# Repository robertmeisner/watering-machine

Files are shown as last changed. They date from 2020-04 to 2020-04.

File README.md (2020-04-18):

# Watering Machine

Modular Watering Machine (Arduino compatible) which allows you to water your crops/plants when needed and provide grow lights on specified interval.

## Introduction

It's an automatic plant watering system or smart irrigation system.

Main functionalities:

- monitors soil moisture with multiple moisture sensors
- waters the plants on specified intervals
- waters plants when soil moisture gets below certain treshold
- turns on grow lights on specified intervals and with specified duration
- allows you to configure and adjust moisture/watering/lighting duration/tresholds

Library aims to be platform agnostic (can be run on Arduino compatible devices: Arduino, ESP32, ESP8266, etc)

Interface with physical layer is separated from Watering Machine "business" logic.
Functions responsible for interfacing with physical infrastructure are injected into components upon their creation.

### States

Watering Machine
Change of states can be triggered with WateringMachine's commands:
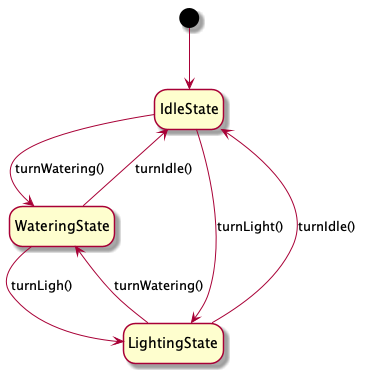
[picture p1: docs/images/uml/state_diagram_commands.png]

or when certain conditions are met:
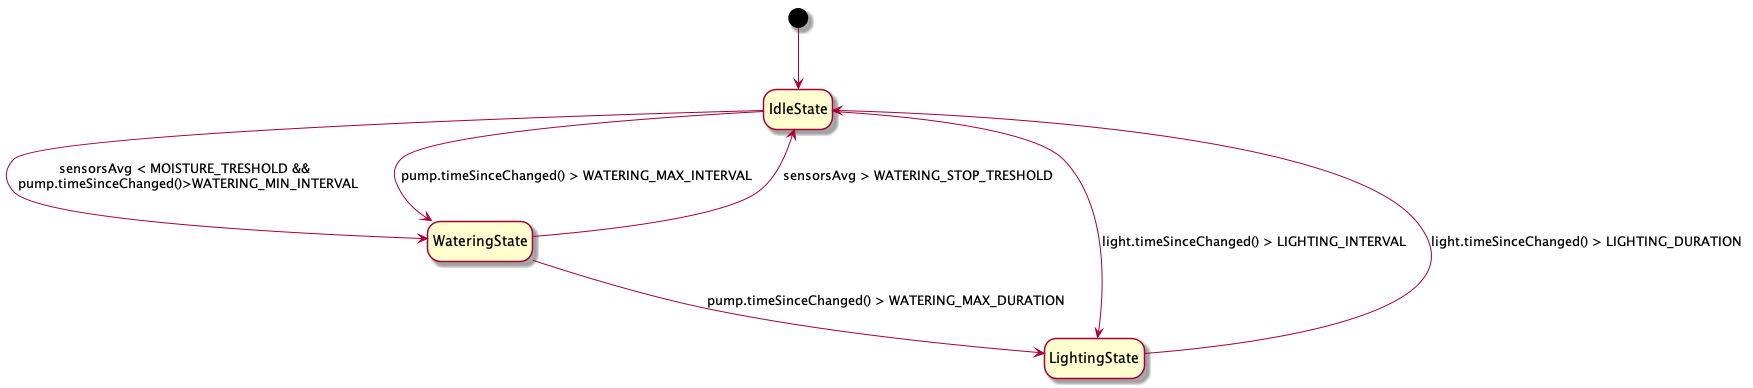
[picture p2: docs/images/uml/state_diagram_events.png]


Note: Lighting and Watering states are separate and cannot occur in parallel.

## Usage guide

### Configuration

Watering Machine behaviour can be cotnroller with the WateringMachineConfig object.
All times are in milliseconds.

Example Arduino code:

```cpp
WateringMachineConfig config;
setup(){
    const unsigned long ONE_HOUR = 1000 * 60 * 60; // hour constant

    config.LIGHTING_DURATION = ONE_HOUR * 8; // How long lighting session should last
    config.LIGHTING_INTERVAL = ONE_HOUR * 16; // Interval between lighting sessions
    config.WATERING_MAX_DURATION = ONE_HOUR /2; // How long watering should last
    config.WATERING_MAX_INTERVAL = ONE_HOUR * 24 * 7; // Maximal interval between waterings. After that time, watering will start even if avarage moisture level from sensors is over the MOISTURE_TRESHOLD
    config.WATERING_MIN_INTERVAL = ONE_HOUR; // Minimal interval between waterings. After watering is done it won't start again, before WATERING_MIN_INTERVAL has passed,even if avarage moisture level from sensors is below the MOISTURE_TRESHOLD
    config.MOISTURE_TRESHOLD = 52; //if avarage moisture level from sensors is below the MOISTURE_TRESHOLD watering starts
    config.WATERING_STOP_TRESHOLD = 80; //watering will stop if avarage moisture level from sensors reaches that value
}
```

### Sensors adjustment

1. Set DebugLevel to Debug: cLogSetDebugLevel(DebugLevel::DEBUG)
2. Run your Watering Machine
3. Check raw value for sensors when put into Water or wet ground, adjust sensorWetRawValue for sensor in ControlFunctions file
4. Check raw value for sensors when hold in Air or put into dry ground, adjust sensorDryRawValue for sensor in ControlFunctions file

### Arduino

### Example code

```cpp

// include components
#include "src/WateringMachine/Components/PulsePump.h"
#include "src/WateringMachine/Components/Light.h"
#include "src/WateringMachine/Components/MoistureSensor.h"
// include State factory (class geenrating states of Watering Machine)
#include "src/WateringMachine/States/StateFactory.h"
// include config class
#include "src/WateringMachine/WateringMachineConfig.h"
// include Watering Machine
#include "src/WateringMachine/WateringMachine.h"
// include Control Functions used to interface with hardware. Those are injected into Components' constructors.
#include "src/Firmware/Arduino/ControlFunctions.v1.h"

// config object instantiated
WateringMachineConfig config;
// pointer to WateringMachine
WateringMachine *wateringMachine;
// create pump object
static PulsePump pump(startPumpFunc, stopPumpFunc, initPumpFunc); //static so they wont be deleted after setup is detroyed
// create light object
static Light light(lightOnFunc, lightOffFunc, lightInitFunc);
/**
 * Arduno setup function
 */
void setup()
{
    // initialize the serial communication:
    Serial.begin(115200);
    const unsigned long ONE_HOUR = 1000 * 60 * 60; // hour constant

    config.LIGHTING_DURATION = ONE_HOUR * 8;          // How long lighting session should last
    config.LIGHTING_INTERVAL = ONE_HOUR * 16;         // Interval between lighting sessions
    config.WATERING_MAX_DURATION = ONE_HOUR / 2;      // How long watering should last
    config.WATERING_MAX_INTERVAL = ONE_HOUR * 24 * 7; // Maximal interval between waterings. After that time, watering will start even if avarage moisture level from sensors is over the MOISTURE_TRESHOLD
    config.WATERING_MIN_INTERVAL = ONE_HOUR;          // Minimal interval between waterings. After watering is done it won't start again, before WATERING_MIN_INTERVAL has passed,even if avarage moisture level from sensors is below the MOISTURE_TRESHOLD
    config.MOISTURE_TRESHOLD = 52;                    //if avarage moisture level from sensors is below the MOISTURE_TRESHOLD watering starts
    config.WATERING_STOP_TRESHOLD = 80;               //watering will stop if avarage moisture level from sensors reaches that value
    // Create sensor objects and add them to a vector
    static std::vector<MoistureSensor> sensors;
    sensors.push_back(MoistureSensor(Sensor1ReadFunc, sensorInitFunc));
    sensors.push_back(MoistureSensor(Sensor2ReadFunc, sensorInitFunc));
    // initialize StafeFactory object
    static StateFactory sf;
    //create a WateringMachine object
    wateringMachine = new WateringMachine(config, sf, light, pump, sensors);
    //init the WateringMachine
    wateringMachine->init();
};
/**
 * Arduino loop function
 */
void loop()
{
    // call tick function every time to handle WateringMachine logic
    wateringMachine->tick();
    // delay 5s
    delay(5000);
};

```

#### Example Schematic and Bill of Material

##### ESP8266

- [ESP8266 Bill of Material with links](./docs/bom/ESP82666_bom.md)

**Schematic:**
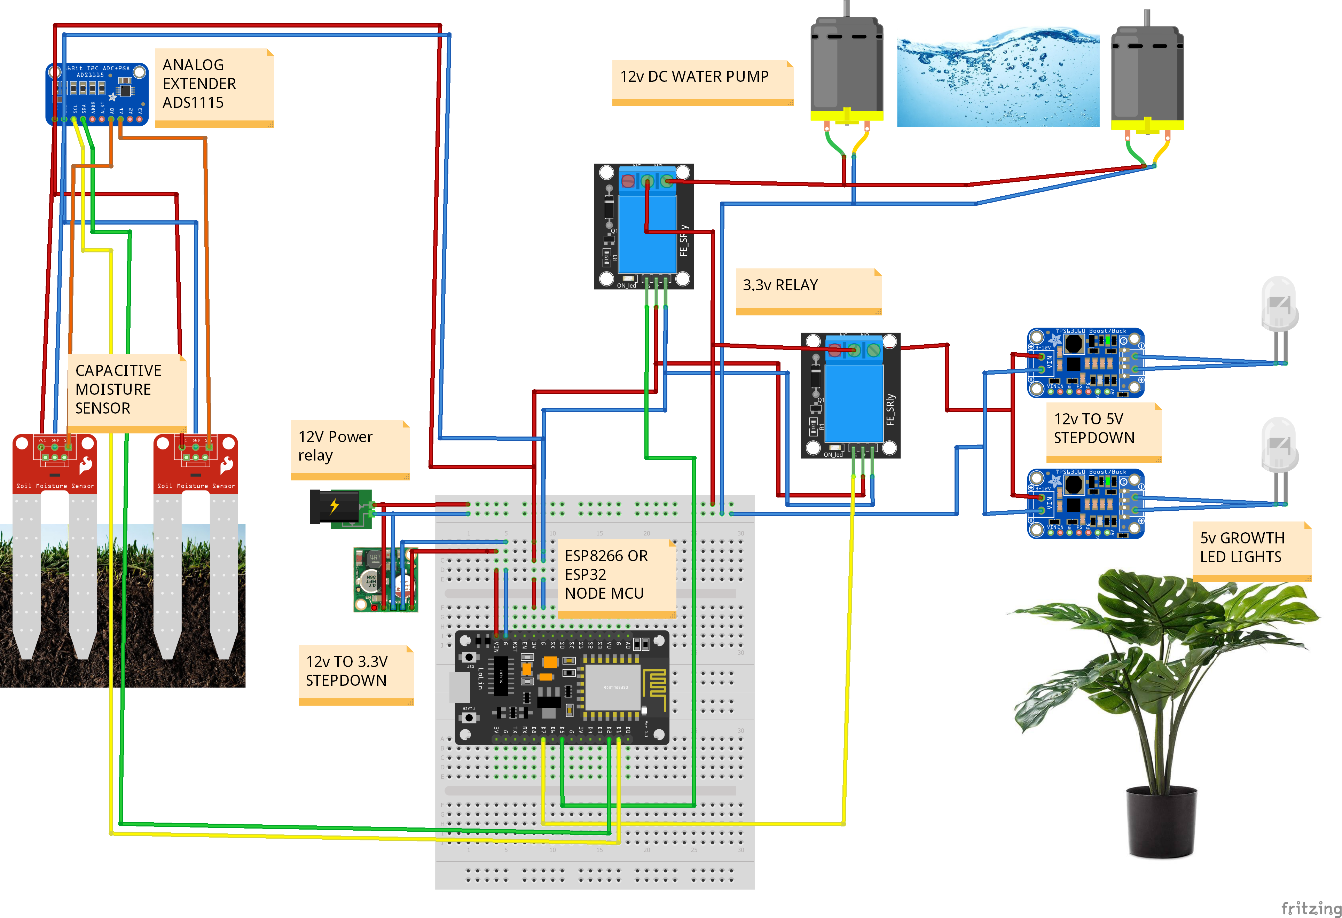
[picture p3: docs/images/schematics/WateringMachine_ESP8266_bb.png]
ESP8266


#### Test/Evaluate/Understand the code

1. Clone or download this repository
2. Uncomment the line // #define WATERING_TEST 1 in watering-machine.ino
3. Open watering-machine.ino inArduino IDE
4. Connect Arduino compatible device to USB port
5. Set port to correct value
6. Click Upload
7. After upload has finished open Serial Terminal and set baud rate to 115200
8. You can see now logs printed by Watering Machine
9. You can experiment with different values returned by Control function, reupload the code and see how this influences the behaviour

#### Run on your own device and setup

1. Build/prototype your Watering Machine (see example Schematic and Bill of Materials)
2. Clone or download this repository
3. Rename root folder e.g. my_watering_machine
4. Duplicate /watering-machine.ino and rename it to mywaterin_machine.ino
5. Copy /src/Firmware/Arduino/ControlFunctions.v[x].h to /libraries/Arduino/ControlFunctions.v[x].h folder
6. change include path of ControlFunctions.v[x].h to the new one
7. Adjust pin numbers in ControlFunctions file to match your build

## Use Cases

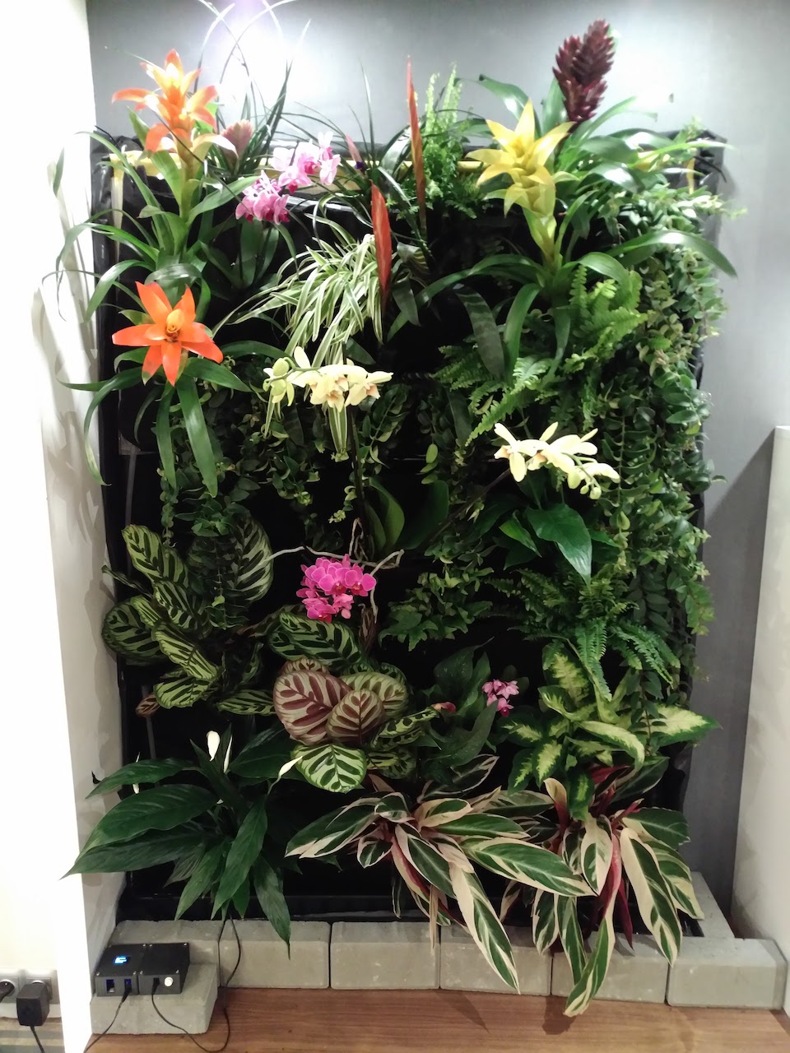
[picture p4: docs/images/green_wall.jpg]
Green Wall in your appartment


## Project structure

``` folder
.
├── docs - documentation and other file assets (images, uml etc)
├── libraries - Here you can place some aditional libraries if needed
├── src - Waterng Machine code
│   ├── Firmware - Control Functions which allow to communicate with a hardware/physical components. Those are injected to component objects upon their creation.
│   │   ├── Arduino - Arduino compatible examples of Control functions
│   │   └── ControlFunctions.Test.h - Test Control Functions to experiment with
│   └── WateringMachine/
│       ├── Components/ - concerte classes of the components (sensors, pump, lights etc.)
│       │   └── StateMachineInterfaces/ - Abstract Component state MAchine classes to be derived by concerte component classes.
│       ├── States/ - Watering MAchine State classes (Watering, Idle, Lighting)
│       ├── Utils/ - Utility classes (logs, formatting, etc. )
│       ├── WateringMachine.cpp
│       ├── WateringMachine.h - main control class of the Watering Machine
│       └── WateringMachineConfig.h 
└── watering-machine.ino - example Arduino sketch with fulll configuration
```

## Improvements and changes

## Questions

For questions about the usage of the libraries, please fill in an issue labeled "question" in Github as that makes it far easier to track them.

## Bugs and issues

For bugs in the libraries, please fill in an issue in Github as that makes it far easier to track them. If possible provide a minimal code snippet that exposes the bug. Also proposals for solutions are welcome.
Issues are not bugs but still possible problematic. E.g. if a library is too slow for your application that is an issue, not a bug. Please fill in an issue and provide as much details about your requirements.

## License and Warranty

Apache License
Version 2.0, January 2004
[http://www.apache.org/licenses/](http://www.apache.org/licenses/)

Please check the file LICENSE and NOTICE for the details.
Give credits a it's requried by the license and if you want to donate, please donate to charity like "doctors without borders".

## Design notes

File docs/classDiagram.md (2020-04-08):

# Class diagrams

## States

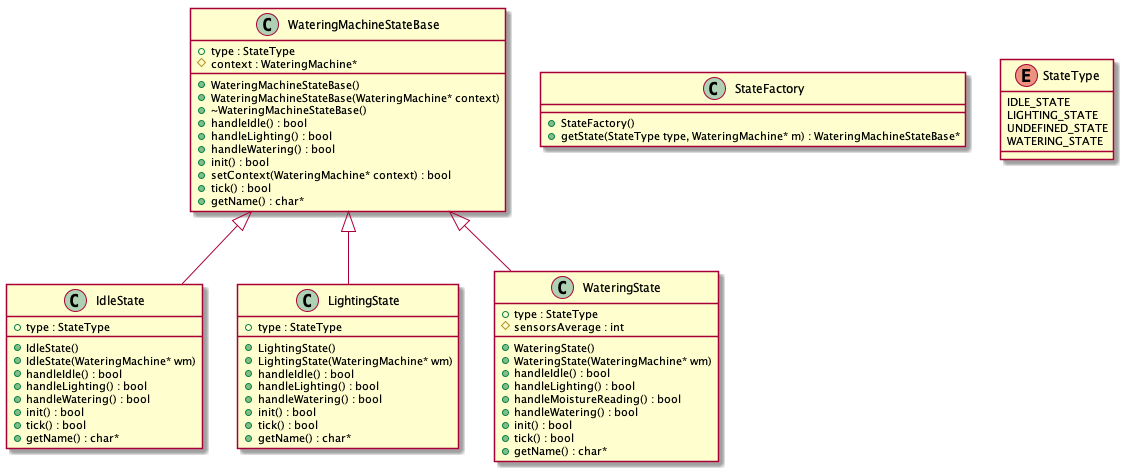
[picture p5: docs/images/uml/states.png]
Watering Machine States Class Diagram

## Components

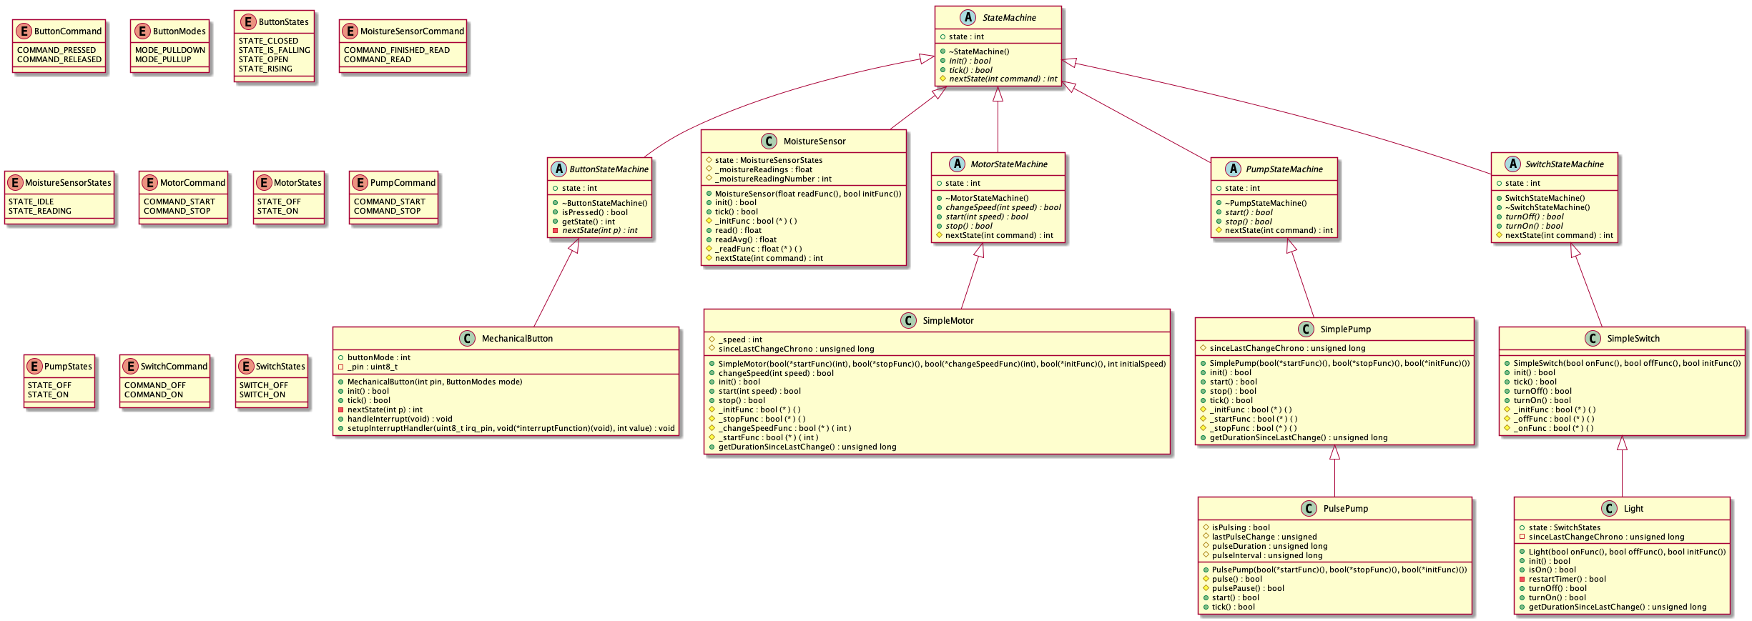
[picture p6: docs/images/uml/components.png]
Watering Machine Components Class Diagram

## Everything

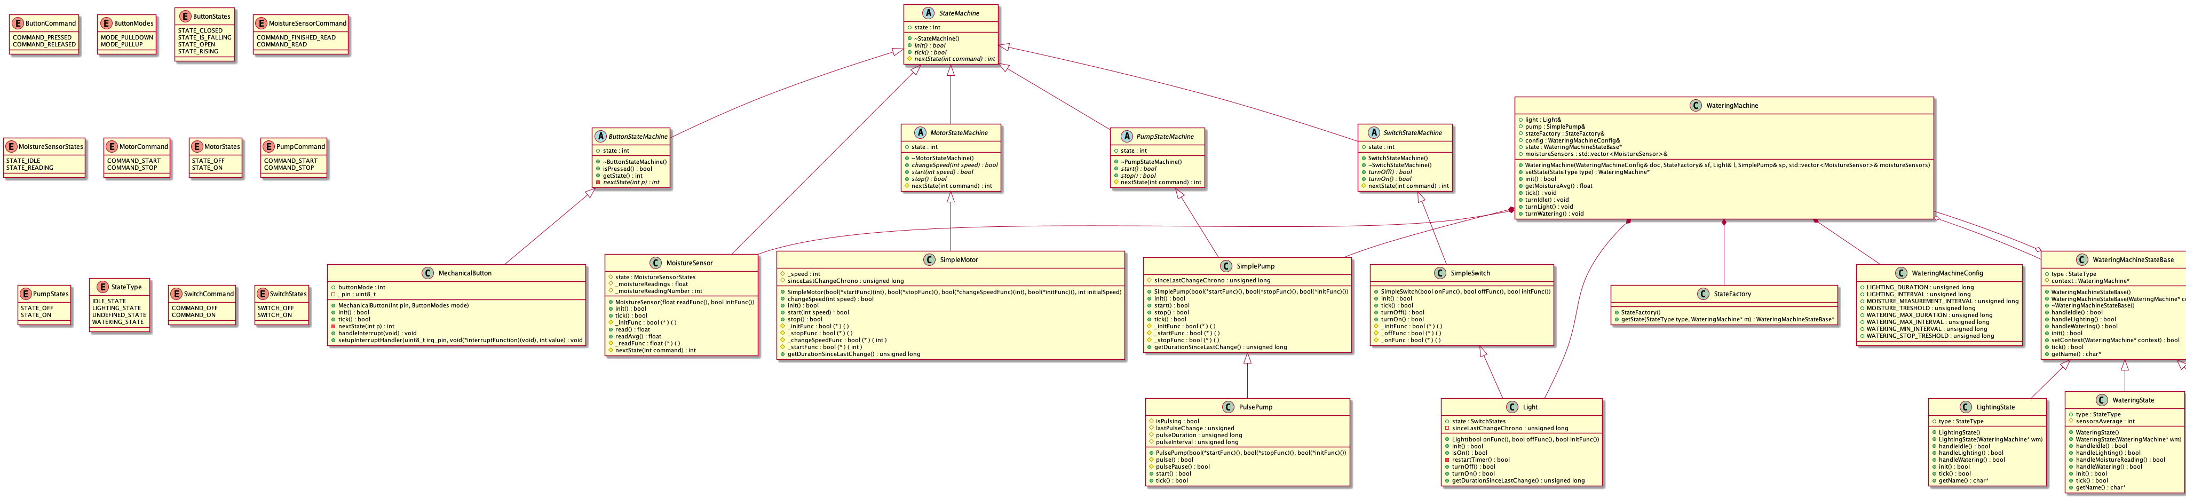
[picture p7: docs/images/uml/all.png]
Watering Machine Class Diagram


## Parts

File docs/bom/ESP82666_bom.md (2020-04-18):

# Greaan Wall + Watering Machine + ESP8266 Node Mcu Bill of Material

*Note:* Below you can find affiliate links, buying from those you support development of this library.

## Water Pump

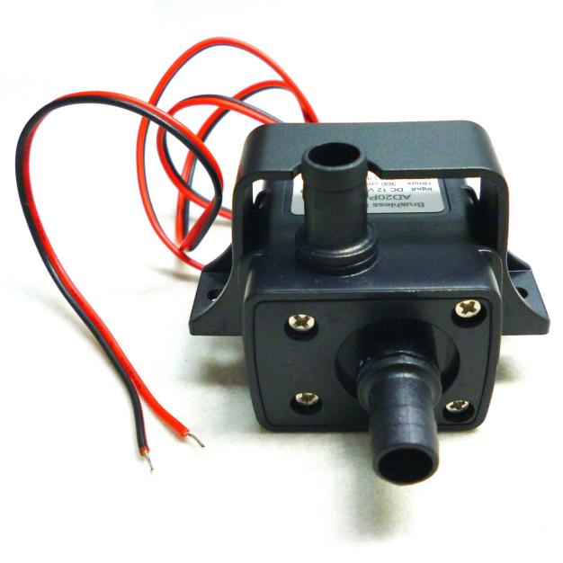
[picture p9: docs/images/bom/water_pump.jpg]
Water Pump 12V


- DC12V pump mini brushless dc submersible pump water cycle cooling [AliExpress.com Product](https://s.click.aliexpress.com/e/_Bf9Lvmsu) </a>

## Moisture sensors

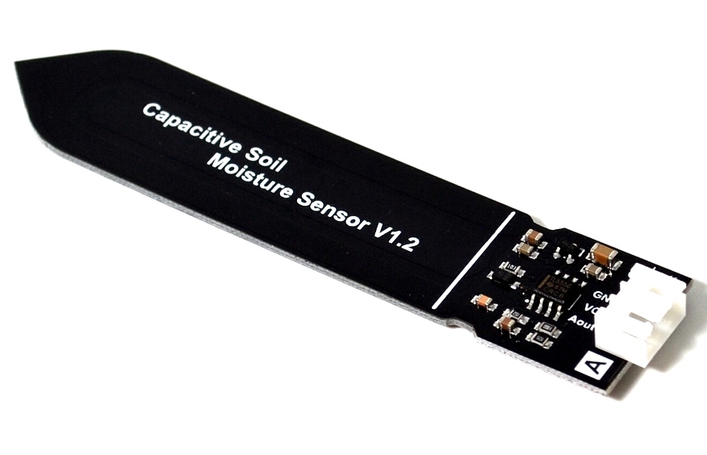
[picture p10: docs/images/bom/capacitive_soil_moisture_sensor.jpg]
Moisture sensors


- Capacitive soil moisture sensor not easy to corrode wide voltage wire for arduino [AliExpress.com Product](https://s.click.aliexpress.com/e/_d76ytBS" target="_parent">AliExpress.com Product - 10pcs</a>

## Analog extender ADS1115

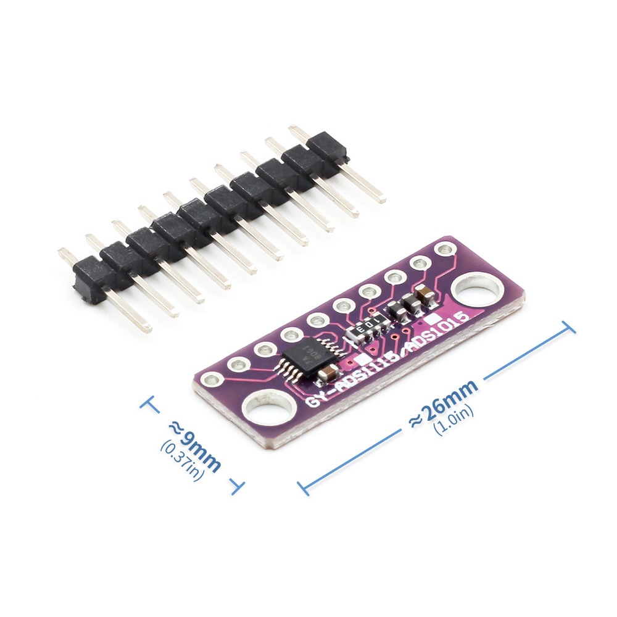
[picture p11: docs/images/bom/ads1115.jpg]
ADS1115


- I2C ADS1115 16 Bit ADC 4 channel Module with Programmable Gain Amplifier 2.0V to 5.5V [AliExpress.com Product](https://s.click.aliexpress.com/e/_dXel4C0)

## 3.3V Relays

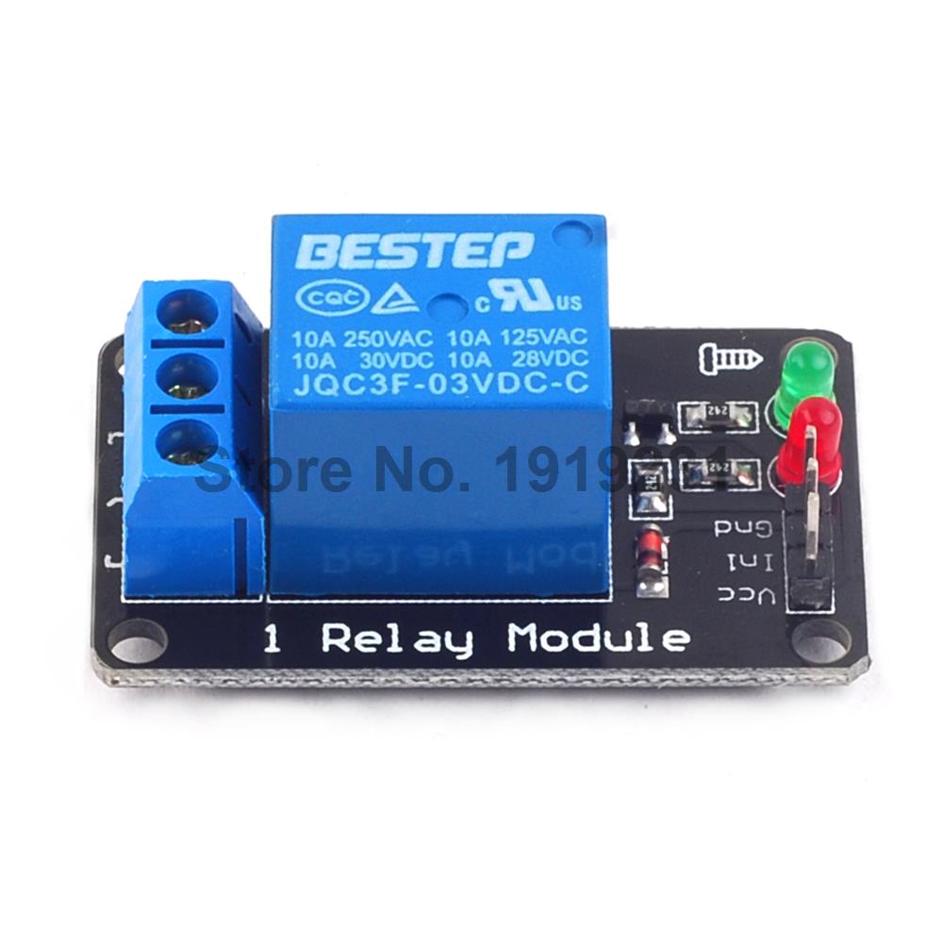
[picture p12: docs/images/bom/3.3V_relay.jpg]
3.3V Relays


- Thyristor AC Switch (relay), 3.3V/5V logic, AC 220V/5A (peak 10A) [AliExpress.com Product](https://s.click.aliexpress.com/e/_d8EjZzI)
- 3.3V 5V 12V 24V Low Level Trigger 1 Channel Relay Module Interface Board Shield for PIC AVR DSP ARM MCU Arduino [AliExpress.com Product](https://s.click.aliexpress.com/e/_dZJLRYU)

## ESP8266 module

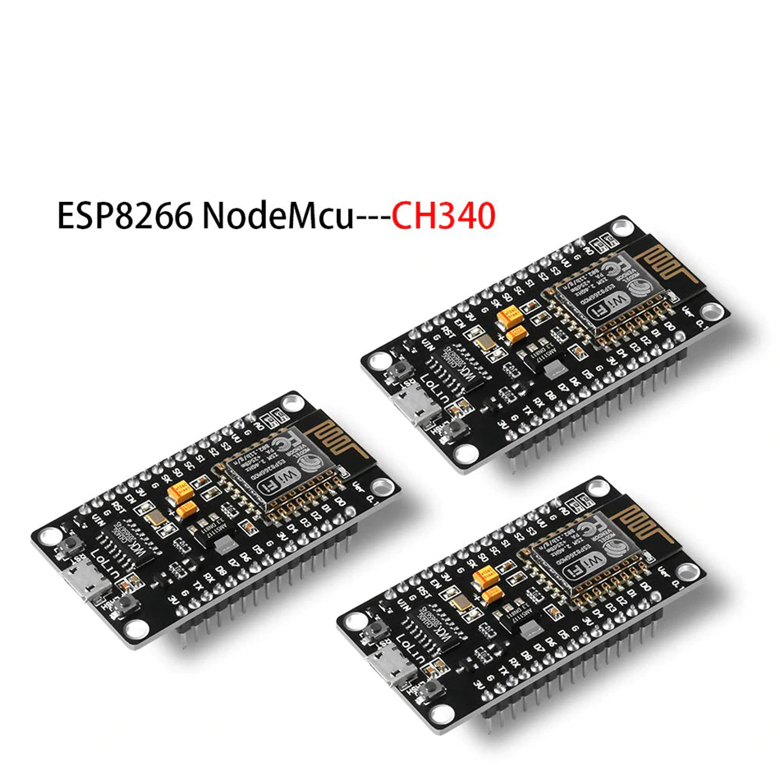
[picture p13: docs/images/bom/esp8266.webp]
ESP8266 module


- L293D Motor Shield Board Wireless Wifi Esp8266 Esp-12E Node MCU Development Kit NodeMCU Rc Toy Remote Control IoT Smart Car [AliExpress.com Product](https://s.click.aliexpress.com/e/_dXiRNkc)
- ESP32 Development Board ESP-32 ESP-32S ESP 32S Lua WiFi Bluetooth Node MCU Board IOT For LuaNode NodeMcu NodeMCU-32S ESP32 S [AliExpress.com Product](https://s.click.aliexpress.com/e/_BfZLenyU)

## ESP8266 development board

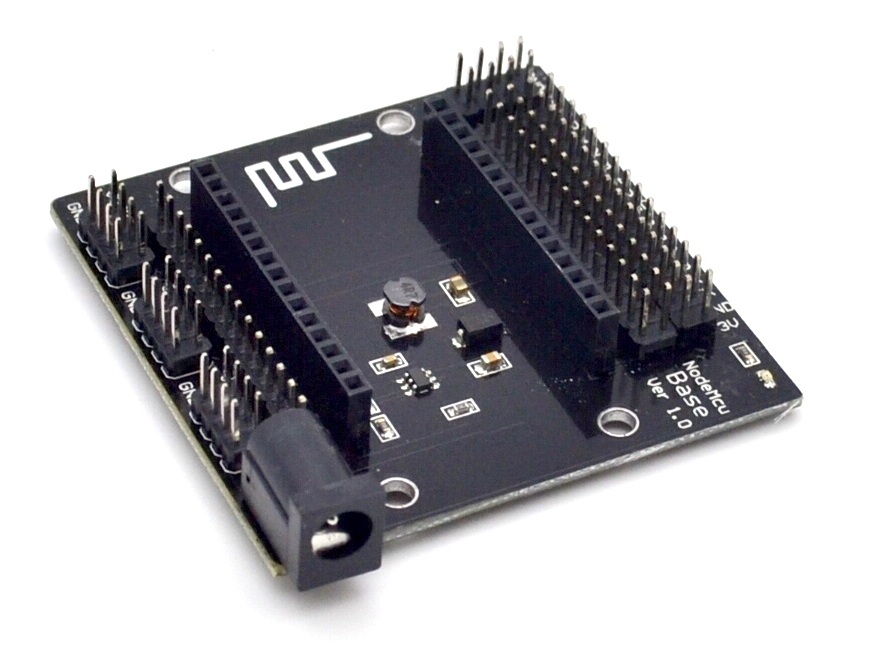
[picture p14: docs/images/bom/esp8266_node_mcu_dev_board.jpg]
ESP8266 development board


- NodeMcu Node MCU Base ESP8266 Testing DIY Breadboard Basics Tester suitable for NodeMcu V3 [AliExpress.com Product](https://s.click.aliexpress.com/e/_d89DjJa)

## 12V power source

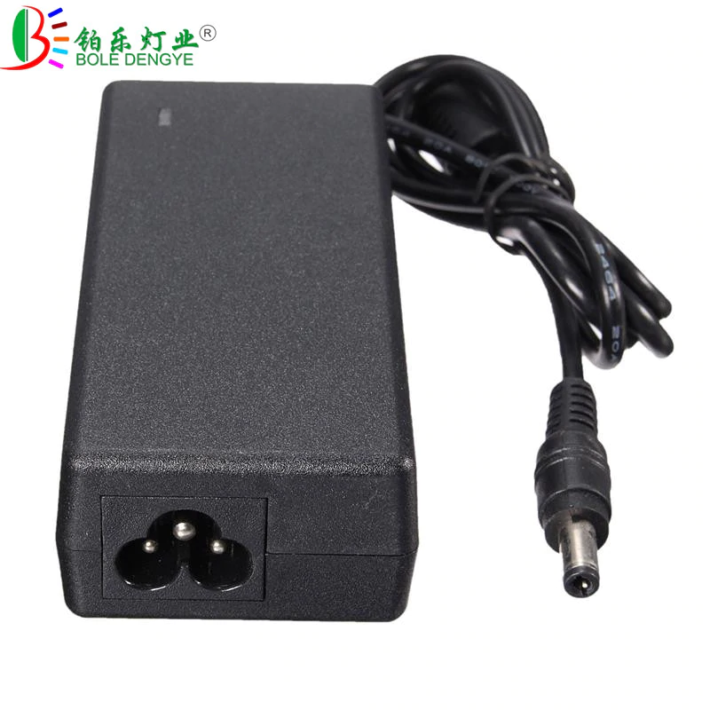
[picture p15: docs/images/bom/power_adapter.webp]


- Power Adapter Supply AC 110V/220V To 12V  Transformer 3A 5A 6A 8A 10A [AliExpress.com Product](https://s.click.aliexpress.com/e/_dWtz1GU)

## 8mm hose, filter and connectors

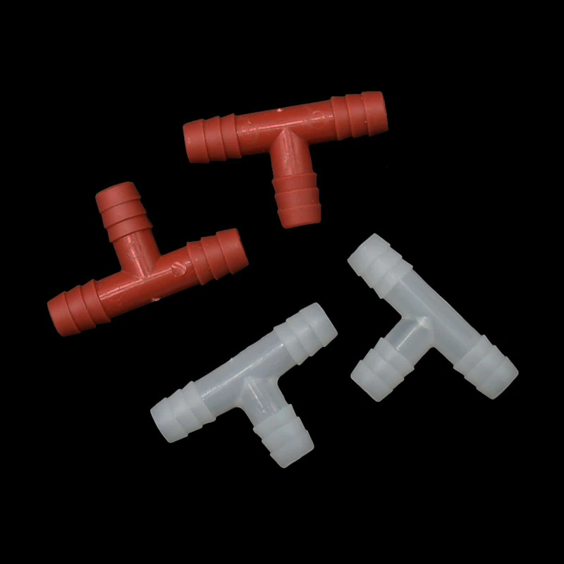
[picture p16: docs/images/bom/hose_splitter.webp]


- T way T-Shape Brass Barb Pipe Hose Fitting 3 way connector For 4mm 5mm 6mm 8mm 10mm 19mm hose copper Pagoda Water Tube Fittings [AliExpress.com Product](https://s.click.aliexpress.com/e/_dV8zvJ6)
- 2pcs Venturi Hose Filter Agricultural Water Purifier Industrial Filter 3 / 8mm Hose Accessory Garden Tools Fountain Accessory [AliExpress.com Product](https://s.click.aliexpress.com/e/_d8sxiRe)
- 3/5mm 4/7mm 8/11mm New PVC Garden Water Hose Irrigation Watering Tubing 1/8'' 1/4'' 3/8'' Black White Blue Transparent Hose [AliExpress.com Product](https://s.click.aliexpress.com/e/_dS1djpq)

## Growth light and stepdown module

ESP8266 development board

- Phytolamps for Plants 5V LED Grow Light Strip 2835 Chip 0.5m 1m 2m LED Phyto Tape for Hydroponic Greenhouse Seedlings Growth [AliExpress.com Product](https://s.click.aliexpress.com/e/_dYde1VQ)
- USB Phytolamps for Plants 5V LED Grow Light Strip 2835 Chip 0.5m 1m 2m LED Phyto Tape for Hydroponic Greenhouse Seedlings Growth [AliExpress.com Product](https://s.click.aliexpress.com/e/_d7z4tj6)
- Plant Grow Light Full Spectrum LED Strip Flower Phyto Lamp Red Blue 10:4 Cultivation Indoor Lamp For Desktop Plant Flower USB UV [AliExpress.com Product](https://s.click.aliexpress.com/e/_d8Ijb2C)
- LM2596s DC-DC step-down power supply module 3A adjustable step-down module LM2596 voltage regulator 24V 12V 5V 3V [AliExpress.com Product](https://s.click.aliexpress.com/e/_dSJVG56)

## Plastic/nylon zip ties

- Self-locking plastic nylon tie 100 PCS black 5X300cable tie fastening ring3X200 cable tie zip wraps strap nylon cable tie [AliExpress.com Product](https://s.click.aliexpress.com/e/_dVu9dCy)

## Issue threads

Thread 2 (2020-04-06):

Improve README.md

robertmeisner, 2020-04-06:
Documentation should include:

- Introduction
- Installation guide
- Improvements and changes
- Questions
For questions about the usage of the libraries, please post a question on???
- Bugs and issues
For bugs in the libraries, please fill in an issue in Github as that makes it far easier to track them. If possible provide a minimal code snippet that exposes the bug. Also proposals for solutions are welcome.
Issues are not bugs but still possible problematic. E.g. if a library is too slow for your application that is an issue, not a bug. Please fill in an issue and provide as much details about your requirements.
- License and Warranty
I appreciate if you give credits when appropriate, and if you want to donate, please donate to charity like "doctors without borders".
Please check the file LICENSE and NOTICE for the details.

robertmeisner, 2020-04-18:
Should add example BoM for esp8266

Closed 2020-04-18.

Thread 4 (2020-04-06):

Fix log message in Watering state

robertmeisner, 2020-04-06:
When moisture sensor average is below MOISTURE_TRESHOLD  the message looks stange:
`Moisture sensor is between MOISTURE_TRESHOLD and WATERING_STOP_TRESHOLD: 80>20<40`
should be
`Moisture sensor is between below: WATERING_STOP_TRESHOLD: 20<80. Watering duration is below WATERING_MAX_DURATION: 120000<33223232`

Closed 2020-04-07.

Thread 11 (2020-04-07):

WiFi interface

robertmeisner, 2020-04-07:
**Is your feature request related to a problem? Please describe.**
I'm always frustrated when i have to connect , WIFI functionality would be nice

**Describe the solution you'd like**

- It should be possible to expose control panel through WIFI with user interface (local http server) or MQTT server (subscribe and publish).
- WIFI should be optional.
- User should be able to:
  - update configuration
  - turn Watering on/off
  - turn Light on/off
  - read sensor values

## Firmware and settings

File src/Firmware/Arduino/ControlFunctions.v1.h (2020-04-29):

#include <Arduino.h>
#include <Wire.h>
#include <Adafruit_ADS1015.h>
// Include custom log library
#include "../../WateringMachine/Utils/CustomLog.h"

#ifndef ArduinoFunctions_h
#define ArduinoFunctions_h
// The ADC input range (or gain) can be changed via the following
// functions, but be careful never to exceed VDD +0.3V max, or to
// exceed the upper and lower limits if you adjust the input range!
// Setting these values incorrectly may destroy your ADC!
//                                                                ADS1015  ADS1115
//                                                                -------  -------
// ads.setGain(GAIN_TWOTHIRDS);  // 2/3x gain +/- 6.144V  1 bit = 3mV      0.1875mV (default)
// ads.setGain(GAIN_ONE);        // 1x gain   +/- 4.096V  1 bit = 2mV      0.125mV
// ads.setGain(GAIN_TWO);        // 2x gain   +/- 2.048V  1 bit = 1mV      0.0625mV
// ads.setGain(GAIN_FOUR);       // 4x gain   +/- 1.024V  1 bit = 0.5mV    0.03125mV
// ads.setGain(GAIN_EIGHT);      // 8x gain   +/- 0.512V  1 bit = 0.25mV   0.015625mV
// ads.setGain(GAIN_SIXTEEN);    // 16x gain  +/- 0.256V  1 bit = 0.125mV  0.0078125mV

//ads.begin(1,0);                // for ESP8266  SDA, SCL can be specified
static Adafruit_ADS1115 ads;
static bool sensorsInitiated = false;
static int sensorRawDryValue1 = 26180;
static int sensorRawWetValue1 = 11436;
static int sensorRawDryValue2 = 26920;
static int sensorRawWetValue2 = 11526;
#define MOISTURE_SENSOR_SAMPLES 5
#define ADS_GAIN GAIN_ONE              // change to GAIN_TWOTHIRDS if using 5V!!!!
#define ADS_SCALE_FACTOR 0.125f / 1000 // adjust scale factor to ADS_GAIN

#define PUMP_PIN 14
#define LIGHTS_PIN 13
#define SENSOR1_PIN 0
#define SENSOR2_PIN 1

bool sensorInitFunc()
{
    if (!sensorsInitiated)
    {
        ads.setGain(GAIN_ONE);
        ads.begin();
        sensorsInitiated = true;
    }
    return true;
}
float _readAds(int pin, String sensorName = "")
{
    float adc = 0;
    int sample_count = 0;
    //additional smoothing
    for (int i = 0; i <= MOISTURE_SENSOR_SAMPLES; i++)
    {
        adc += ads.readADC_SingleEnded(pin);
        delay(50);
    }
    adc = adc / MOISTURE_SENSOR_SAMPLES;
    cLog("Moisture Sensor| " + sensorName + " Raw Value: " + String(adc),DebugLevel::DEBUG);
    float volts = adc * ADS_SCALE_FACTOR;
    cLog("Moisture Sensor| " + sensorName + " Volts Value: " + String(volts),DebugLevel::DEBUG);
    if (sensorName == "Sensor #1")
    {
        adc = constrain(adc, sensorRawWetValue1, sensorRawDryValue1); // Keep the ranges!
        adc = map(adc, sensorRawWetValue1, sensorRawDryValue1, 100, 0);
    }
    else
    {
        adc = constrain(adc, sensorRawWetValue2, sensorRawDryValue2); // Keep the ranges!
        adc = map(adc, sensorRawWetValue2, sensorRawDryValue2, 100, 0);
    }
    return adc;
}

float Sensor1ReadFunc()
{
    return _readAds(SENSOR1_PIN, "Sensor #1");
}
float Sensor2ReadFunc()
{
    return _readAds(SENSOR2_PIN, "Sensor #2");
}

bool startPumpFunc()
{
    digitalWrite(PUMP_PIN, LOW);
    return true;
}
bool stopPumpFunc()
{
    digitalWrite(PUMP_PIN, HIGH);
    return true;
}
bool initPumpFunc()
{
    pinMode(PUMP_PIN, OUTPUT);
    stopPumpFunc();
    return true;
}

bool lightOnFunc()
{
    digitalWrite(LIGHTS_PIN, LOW);
    return true;
}
bool lightOffFunc()
{
    digitalWrite(LIGHTS_PIN, HIGH);
    return true;
}
bool lightInitFunc()
{
    pinMode(LIGHTS_PIN, OUTPUT);
    lightOffFunc();
    return true;
}
#endif

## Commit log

2020-04-11 Adjusted default sensors sensitivity and changed config value.
2020-04-11 adjusted pulse pump timing
2020-04-13 remove unused and unfinished Mechanical button
2020-04-13 remove unused display component and button state machine
2020-04-13 adds debug messaging filtering related to #1
2020-04-14 #9 initial esp8266 schematic
    [WateringMachine_ESP8266.fzz]
2020-04-14 update schematic and esp8266 pinout
    related to #9
    [WateringMachine_ESP8266.fzz]
2020-04-15 updated schematic and generated image
    [WateringMachine_ESP8266.fzz]
2020-04-18 Added example schematics
    fixes #9
    [WateringMachine_ESP8266.fzz]
2020-04-18 Added ESP8266 BoM
    fixes #10
2020-04-18 change naming of raw and dry limits for sensors
2020-04-18 fix comments and doc
    fixes #2
    [watering-machine.ino]
2020-04-18 Update Schematic
    [WateringMachine_ESP8266.fzz]
2020-04-23 Added notes and pictures to schematic fixes #21, fixes #20
    [WateringMachine_ESP8266.fzz]
2020-04-29 adjust sensor values
